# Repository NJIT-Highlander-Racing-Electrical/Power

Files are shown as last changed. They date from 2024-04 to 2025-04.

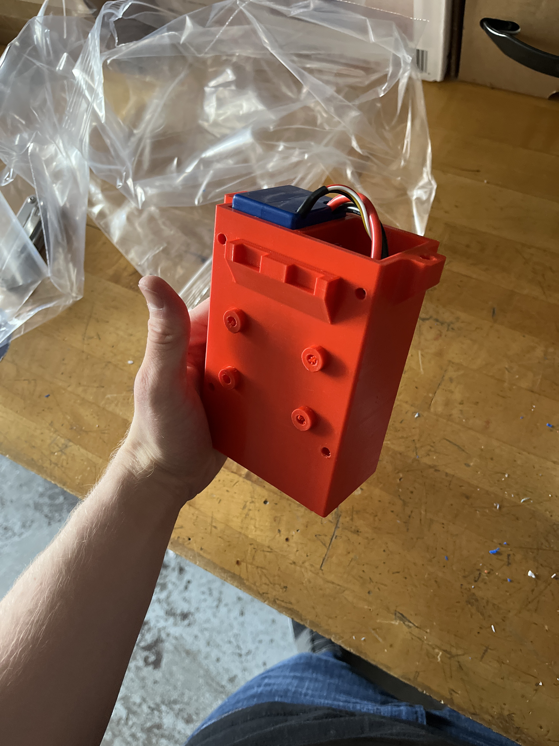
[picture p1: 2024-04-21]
Photos/IMG_0790.JPG

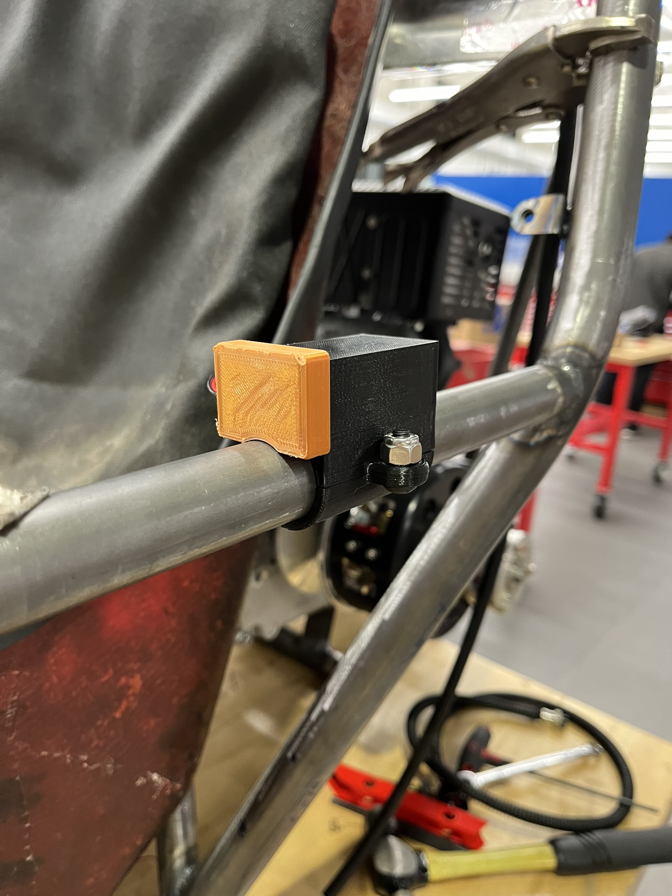
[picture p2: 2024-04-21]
Photos/IMG_1284.JPEG

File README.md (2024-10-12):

# Power

A repository dedicated to everything power-related: batteries, connectors, wiring, battery management, systems, and more.

## Batteries

* Zippy 5000mAh 11.1v batteries
  * Can be ran in parallel after balancing for extra capacity
  * Housed in a 3D printed dual battery holder
  * Two thumb screws lock the batteries into place with a cover bar
* Battery Management System
  * Uses a Low Voltage Disconnect Module to cut off battery power when battery voltage gets too low
  * Ideally includes short circuit protection or fuse

## Wiring

* 14 AWG wire for main power bus connections
* 24 AWG wire to split off to smaller subsystems 
* CAN-Bus signals are sent over 24 AWG twisted pair wire
* All subsystems use 4-pin Aviation Plug Connectors for 12V power and CAN-Bus signals

## Voltage Regulation at Subsystems

* All subsystems will have a 5V switching regulators
   * Running the vehicle power bus at 12V but each subsystem only requiring 5V allows for a voltage drop on the bus without issues
   * Switching regulators are far more efficient than linear regulators, which would get too hot stepping down from 12V to 5V at higher loads
   * The ESP32 can also output 3.3V from the 5V we supply if needed for its subsystems

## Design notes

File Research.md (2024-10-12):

# Research

## Idea 1

LM2576 IC TO 263 package
  - Add complementary passive components to make our own 5V buck converter
  - Connector XT-30 connectors

### Pros:
* Cost under 5 dollars per piece (if we make over 10).
### Cons:
* Complexity

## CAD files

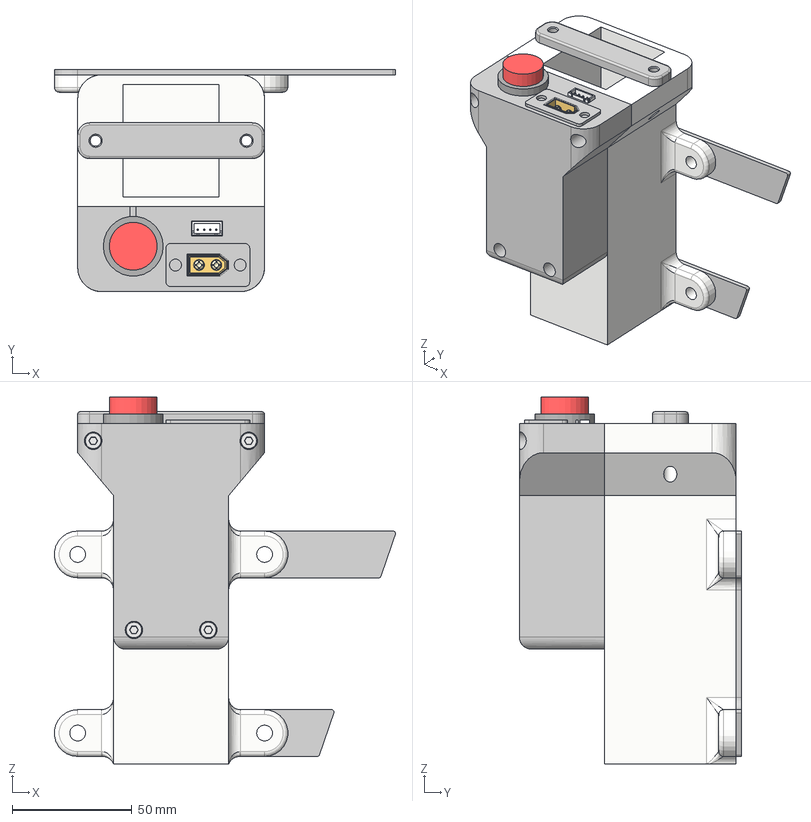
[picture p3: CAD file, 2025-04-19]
3D Models/Battery Box.step
142.4 x 92.8 x 153.1 mm
XT60 Female v2
4 Pin JST Connector
M4 CUP HEAD SCREW x 4
insert x 4

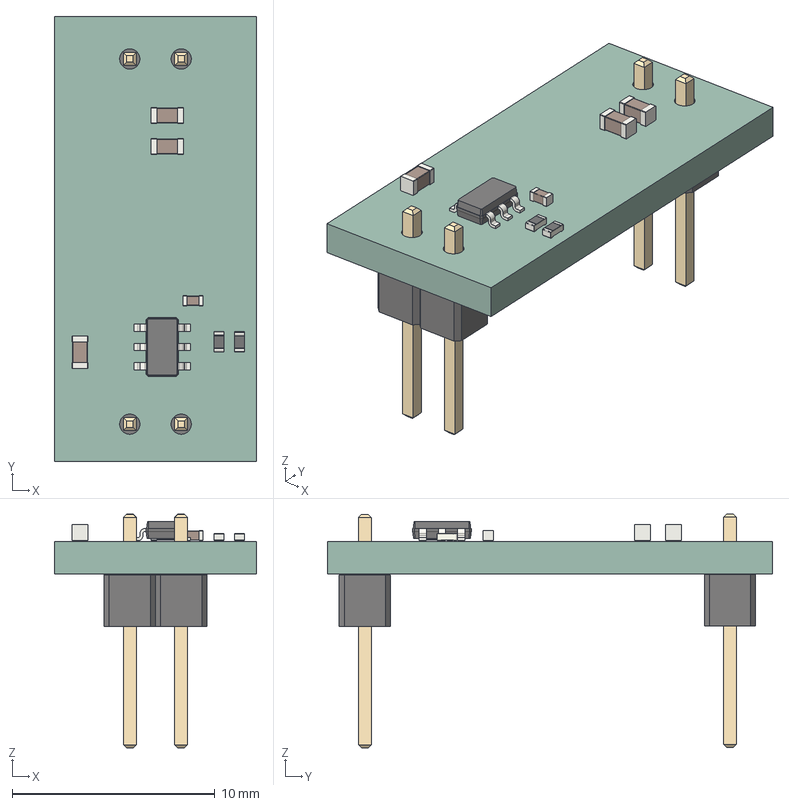
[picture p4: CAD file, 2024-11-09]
3D Models/12V-5V Voltage Regulator 3D Model.step
10.0 x 22.0 x 11.6 mm
C_0603_1608Metric x 3
PinHeader_1x02_P254mm_Vertical x 2
R_0402_1005Metric x 2
TSOT_23_6
C_0402_1005Metric
5v buck pt iii_PCB

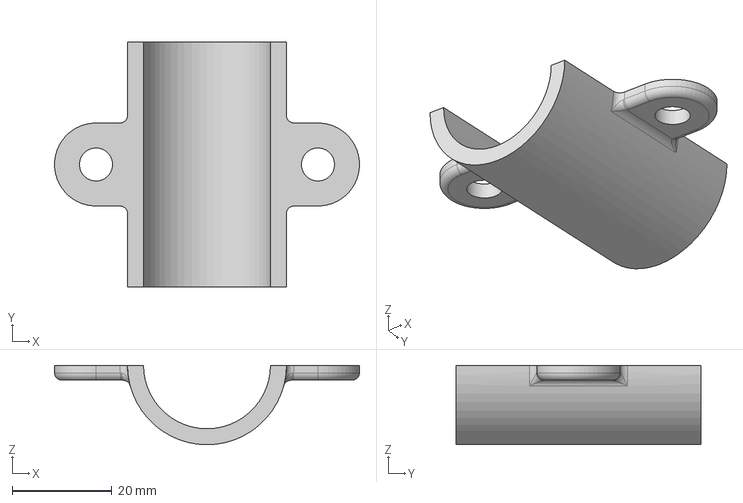
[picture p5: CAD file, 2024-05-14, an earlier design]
2023-2024 Archive/3D Models/Brake Light 9V Battery Clamshell Bottom Half.step
61.0 x 49.0 x 15.9 mm

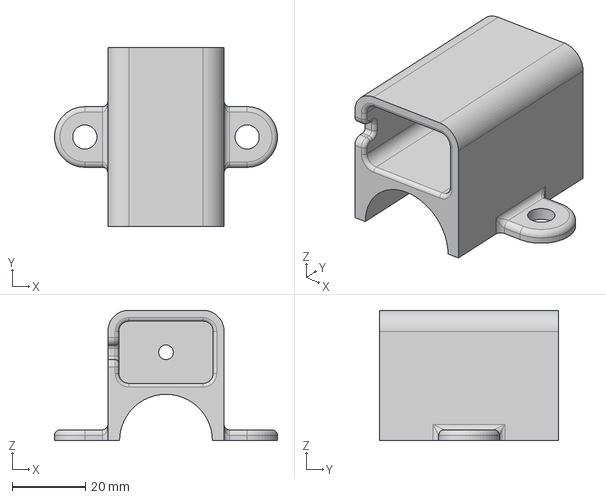
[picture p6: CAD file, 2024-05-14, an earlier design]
2023-2024 Archive/3D Models/Brake Light 9V Battery Clamshell Top Half.step
61.0 x 49.0 x 35.7 mm

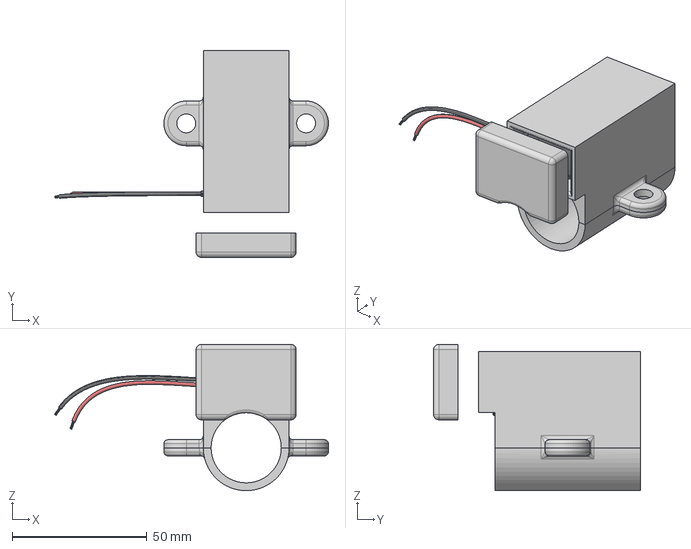
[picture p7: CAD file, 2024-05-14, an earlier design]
2023-2024 Archive/3D Models/Brake Light 9V Battery Clamshell.step
101.5 x 76.7 x 54.3 mm
9V Battery
9V Battery Clip Connector

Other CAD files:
2023-2024 Archive/3D Models/Battery Holder V2 v22.f3d
3D Models/Battery Box.f3z
3D Models/Battery Holder V2 v22.f3d

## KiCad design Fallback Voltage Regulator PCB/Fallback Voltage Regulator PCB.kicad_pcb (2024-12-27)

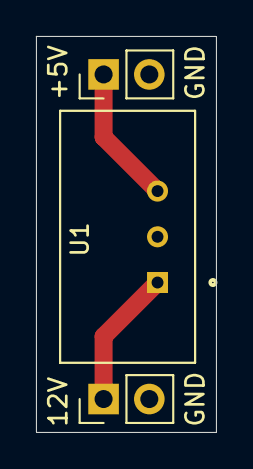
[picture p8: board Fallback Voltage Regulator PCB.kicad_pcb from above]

Board: 2 copper layers, 10.0 x 22.0 mm, 3 parts (0 on the bottom side), 3 nets.

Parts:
J1, J2: Conn_01x02; PinHeader_1x02_P2.54mm_Vertical
U1: TR10S05-Voltage-Regulator; TR10S05

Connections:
/+12V: J1.1, U1.1 (VIN)
GND: J1.2, J2.2, U1.2 (GND)
unnamed: J2.1, U1.3 (VOUT)

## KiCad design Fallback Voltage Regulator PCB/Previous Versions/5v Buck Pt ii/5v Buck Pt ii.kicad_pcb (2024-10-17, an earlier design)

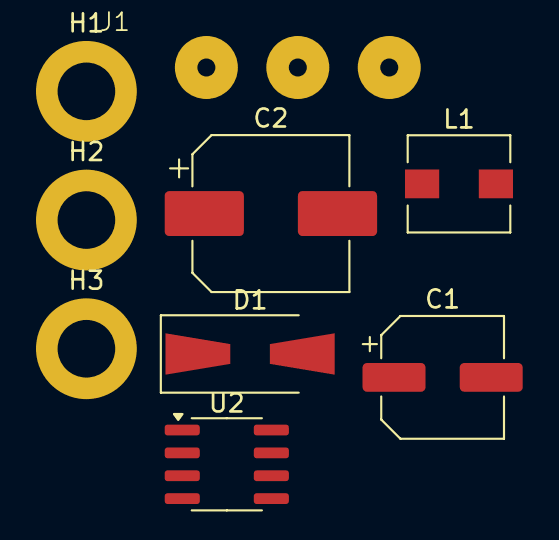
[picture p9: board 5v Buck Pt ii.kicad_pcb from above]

Board: 2 copper layers, 9 parts (0 on the bottom side), 4 nets, no tracks yet.

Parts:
C1: 100 uF; CP_Elec_6.3x5.4_Nichicon
C2: 1000 uF; CP_Elec_8x10.5
D1: 1N5822; D_SMA-SMB_Universal_Handsoldering
H1, H2, H3: MountingHole_Pad; MountingHole_3.2mm_M3_DIN965_Pad
J1: Conn_01x03_Pin; cast
L1: 100 uH; L_Wuerth_HCI-5040
U2: GL2576-5.0SF8DR; SOIC-8_3.9x4.9mm_P1.27mm

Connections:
+5V: C2.1, H3.1, J1.1, L1.2, U2.3 (FB)
+15V: C1.1, H1.1, J1.3, U2.1 (VIN)
GND: C1.2, C2.2, D1.2 (A), H2.1, J1.2, U2.4 (~ON/OFF), U2.5 (GND), U2.6 (GND), U2.7 (GND), U2.8 (GND)
unnamed: D1.1 (K), L1.1, U2.2 (VOUT)

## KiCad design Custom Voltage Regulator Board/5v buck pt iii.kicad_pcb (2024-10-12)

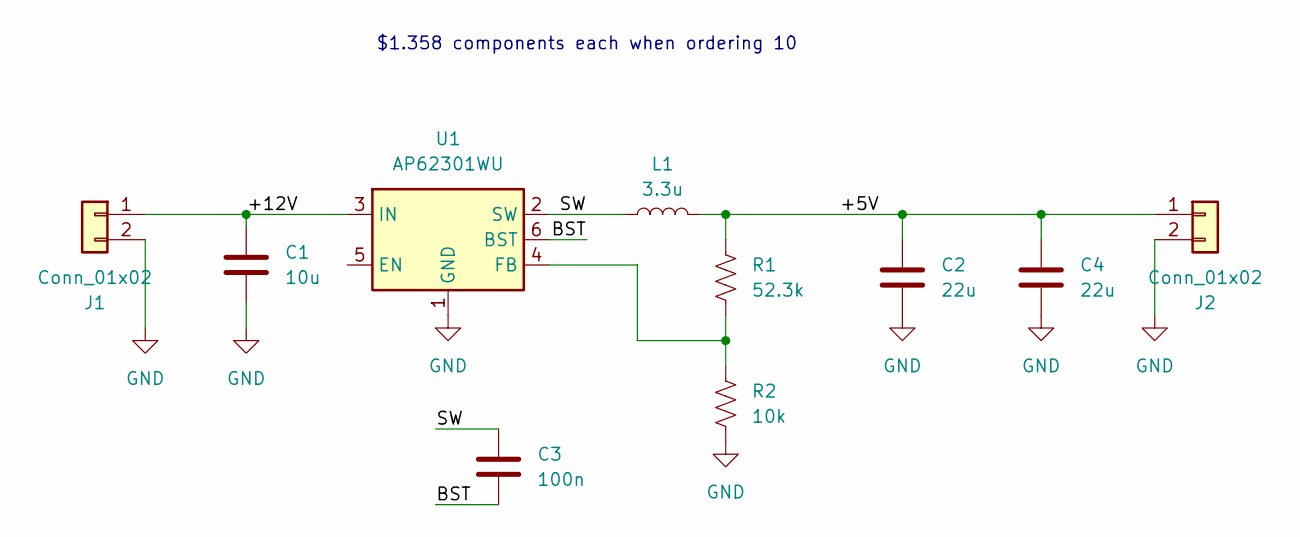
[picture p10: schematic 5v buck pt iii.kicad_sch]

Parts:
C1: 10u; C_0603_1608Metric
C2, C4: 22u; C_0603_1608Metric
C3: 100n; C_0402_1005Metric
J1, J2: Conn_01x02; PinHeader_1x02_P2.54mm_Vertical
L1: 3.3u; L_Taiyo-Yuden_NR-50xx
R1: 52.3k; R_0402_1005Metric
R2: 10k; R_0402_1005Metric
U1: AP62301WU; TSOT-23-6

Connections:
/+5V: C2.1, C4.1, J2.1, L1.2, R1.1
/+12V: C1.1, J1.1, U1.3 (IN)
/BST: C3.2, U1.6 (BST)
/SW: C3.1, L1.1, U1.2 (SW)
GND: C1.2, C2.2, C4.2, J1.2, J2.2, R2.2, U1.1 (GND)
unnamed: R1.2, R2.1, U1.4 (FB)

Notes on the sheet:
$1.358 components each when ordering 10

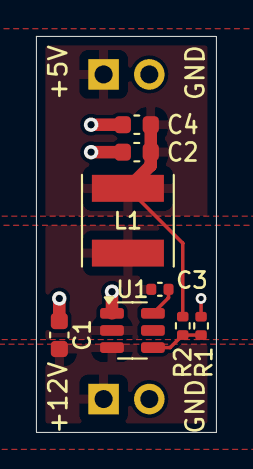
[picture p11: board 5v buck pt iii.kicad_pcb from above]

Board: 2 copper layers, 10.0 x 22.0 mm, 10 parts (0 on the bottom side), 6 nets.

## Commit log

2024-02-07 Add files via upload
    Rough sketch of wiring in car. Blue squares represent XT60 connectors breaking off of the main power bus. The purpose of these is to allow for us to adjust the length of the wires connecting the subs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
2024-04-04 Update and rename Brake Light 9V Battery Clamshell Top Half.step to Brake Light Power/Brake Light 9V Battery Clamshell Top Half.step
    [Brake Light 9V Battery Clamshell Top Half.step]
2024-04-04 Update and rename Brake Light 9V Battery Clamshell Bottom Half.step to Brake Light Power/Brake Light 9V Battery Clamshell Bottom Half.step
    [Brake Light 9V Battery Clamshell Bottom Half.step]
2024-04-17 Rename Battery Holder V2 v22.f3d to Battery-Holder/Battery Holder V2 v22.f3d
    [Battery Holder V2 v22.f3d]
2024-04-21 Update and rename Brake Light Power/Brake Light 9V Battery Clamshell Bottom Half.step to Brake Light Power/3D Models/Brake Light 9V Battery Clamshell Bottom Half.step
    [Brake Light 9V Battery Clamshell Bottom Half.step]
2024-04-21 Update and rename Brake Light Power/3D Models/Brake Light 9V Battery Clamshell Bottom Half.step to 3D Models/Brake Light 9V Battery Clamshell Bottom Half.step
    [Brake Light 9V Battery Clamshell Bottom Half.step]
2024-04-21 Update and rename Brake Light 9V Battery Clamshell Top Half.step to Brake Light 9V Battery Clamshell Top Half.step.
2024-04-21 Update and rename Brake Light 9V Battery Clamshell.step to Brake Light 9V Battery Clamshell.step
    [Brake Light 9V Battery Clamshell.step]
2024-04-21 Update and rename Brake Light 9V Battery Clamshell Top Half.step. to Brake Light 9V Battery Clamshell Top Half.step
    [Brake Light 9V Battery Clamshell Top Half.step]
2024-04-21 organized project files
    [Battery Holder V2 v21.f3d, Battery Holder V2 v22.f3d, Battery Holder.f3d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]
2024-05-14 moving 2023-2024 files to archive
    [Battery Holder V2 v22.f3d, Brake Light 9V Battery Clamshell Bottom Half.step, Brake Light 9V Battery Clamshell Top Half.step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]
2024-10-12 add 5v buck part 3
    [5v buck pt iii.kicad_pcb, 5v buck pt iii.kicad_sch]
2024-10-17 Rename 5v buck pt iii/5v buck pt iii.kicad_pcb to 5v buck pt iii/Custom Voltage Regulator Board/5v buck pt iii.kicad_pcb
    [5v buck pt iii.kicad_pcb]
2024-10-17 Rename 5v buck pt iii/Custom Voltage Regulator Board/5v buck pt iii.kicad_pcb to Custom Voltage Regulator Board/5v buck pt iii.kicad_pcb
    [5v buck pt iii.kicad_pcb]
2024-10-17 Rename 5v buck pt iii.kicad_prl to 5v buck pt iii.kicad_prl
2024-10-17 Rename 5v buck pt iii.kicad_pro to 5v buck pt iii.kicad_pro
2024-10-17 Rename 5v buck pt iii.kicad_sch to 5v buck pt iii.kicad_sch
    [5v buck pt iii.kicad_sch]
2024-10-17 Organize Files
    [5v Buck Pt ii.kicad_pcb, 5v Buck Pt ii.kicad_sch]
2024-12-12 Add battery box
2024-12-27 Add fallback voltage regulator board that uses TR10S05 Regulator
    [5v Buck Pt ii.kicad_pcb, 5v Buck Pt ii.kicad_sch, Fallback Voltage Regulator PCB.kicad_pcb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]
2024-12-28 Add GBR and DRL files for fallback pcb
2025-01-05 Update Battery Box Model
2025-04-19 Update 3D models
    [Battery Box.f3z, Battery Box.step]
